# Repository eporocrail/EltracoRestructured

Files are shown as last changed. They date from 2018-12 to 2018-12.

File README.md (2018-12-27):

  Aim is to develop a switching and signaling system for model railroad track control.
  Communication is wireless.

  To disconnect the decoder from the controlling software in space and time the MOSQUITTO
  MQTT broker is used.

  Hardware setup is as simple as possible. In stead of having one hardware module for diffferent applications
  the design aims for three different PCB's specific to task where the Wemos has to be slotted into.

  Sofware is modularised. It is gathered into one software package. The functionality of each separate decoder
  is configured by means of a website genrated by the decoder.

  *********************************************************************************************

  Target platform is Wemos D1 mini.

  11 digital input/output pins, all pins have interrupt/pwm/I2C/one-wire supported(except D0)
  1 analog input(3.2V max input)
  a Micro USB connection
  compatible with Arduino IDE.
  pins are active LOW but the Arduino IDE inverts this.

  All of the IO pins run at 3.3V:
  A levelshifter or voltage divider is required.

  For a relay a pin is followed by a transistor/IC. A relay is driven with 5V.

  For a sensor or servo each pin is followed by a 330R resistor to limit current to 10 mA.

  eltraco decoder     Function

  eltraco sensor decoder    Scanning 9 sensors
  eltraco switch decoder    Controlling 8 outputs
  eltraco turnout decoder   Controlling 2 turnouts

  GPIO usage:

  Decoder  pins     function

  Sensor   D0 .. D7     digital sensor
  
           A0           analogue sensor

  Switch   D0 .. D7     output (switch)

  Double   D0    relais 1
  
  Turnout  D1    current detector 1
           
           D2    current detector 2
           
           D3    not used
           
           D4    not used
           
           D5    relais 2
           
           D6    servo 1
           
           D7    servo 2
           
           D8    not used
           
           A0    not used
           
  Single   D0    relais 1
  
  Turnout  D1    current detector 1
           
           D2    sensor
           
           D3    sensor
           
           D4    sensor
           
           D5    sensor
           
           D6    servo 1
           
           D7    not used
           
           D8    not used
           
           A0    not used         

  ROCNET PROTOCOL

  packet payload content:
  byte 1  : groupId
  
  byte 2  : receiveIdH
  
  byte 3  : receiveIdL
  
  byte 4  : sendIdH
  
  byte 5  : sendIdL
  
  byte 6  : group
  
  byte 7  : code
  
  byte 8  : length
  
  byte 9  : data1
  
  byte 10 : data2
  
  byte 11 : data3
  
  byte 12 : data4

  --byte 1 only used for large network. Normally 0.

  --byte 2 only used when more than 255 decoders. Normally 0.

  --byte 3 Rocrail Server default Id is 1

  Broadcast Id = 0
  
  Decoder   Id = 2 ... 255   Not used for switching decoder

  --byte 4 only used when more than 255 decoders. Normally 0.

  --byte 5 Rocrail Server default Id is 1

  Decoder Id   = 2 ... 255 with restrictions as described under "addressing"

  --byte 6

  groups
  code   description     remark                     MQTT topic
  
  0      Host            Rocrail                    rocnet/ht
  
  7      Clock Fast      Clock                      rocnet/ck
  
  8      Sensor          Position determination     rocnet/sr
  
  9      Output                                     rocnet/ot

  --byte 7

  Code:  bit 7 = 0
  
     bit 6 and bit 5 represent Type of code
     
     bit 4 .. 0:  5 bit command 0 .. 31

  Type: 0 - test
  
  1 - request
  
  2 - event
  
  3 - reply

  Sensor

  Actions
  code description data 1  data 2  data 3  data 4  data n
  1    report      addrH¹  addrL¹  status  port    identifier (RFID)

  ¹) Address of the reporting loco.
  The sensor ID is set in the header; Sender.

  Output

  Type   Value
  
  switch   0
  
  light    1
  
  servo    2

  Actions
  code description data 1  data 2  data 3
  
  0      off       type    value   address
  
  1      on        type    value   address

  --byte 8 Netto number of following data bytes.

  At a speed of 200 KmH a loc runs 64 mm per second in scale H0 and 35 mm per second in scale N.
  To come to a reliable detection reaction a point sensor must be scanned at least 20 times per second in H0
  and at least 10 times per second in scale N.

  For scale H0 scan delay should be not larger than 50 miliseconds and for scale N not larger
  than 100 miliseconds. Default will be 20.

  The Wemos Module needs no 3.3V power supply. To the 5V pin external powersupply can be connected.

  Addressing:

  Addressing falls apart in a WiFi address, being an IP-address and a Rocnet address.

  Rocnet:

  In the Rocnet protocol (IdH*256 + IdL) represents the Rocnet Node Number. This number ranges from 1 .. 65536.
  It represents the "Bus" number.
  Depending on the function performed the I/O pin of the decoder is addressed with "data3" for
  "output" functions or "data4" for "sensor" functions. Turnouts are controlled with an "output" function.
  The values of data3/data4 are in rocrail inserted in field "Address"

  For eltraco an I/O pin is addressed by the combination of receiveIdL and data3/data4.
  This way each individual pin of each individual decoder can be addressed.

  A second way to address an IO pin is using a "fixed" receiveIdL and discriminating by means of data3/data4.
  Using this method provides in eltraco the possibility to address 255 turnouts by a consecutive number only.
  The default receiveIdL of Rocrail is "9". This receiveIdL is used to control turnouts. These addresses are
  used by the servo-tool to adjust the servo of a turnout.

  IP-address:
  The following IP-adress range is available:
  192.168.xxx.xxx

  IP-addres: Router 192.168.xxx.251
  
             Configuration website 192.168.xxx.252
             
             Command Station       192.168.xxx.253
             
             Mosquitto             192.168.xxx.254

  For the decoders are available 192.168.xxx.2 - 192.168.2.250

  Each decoder is allocated a unique IP-address out of the range 192.168.xxx.2 - 192.168.2.250.
  The last triplet is the Rocrail "Bus" number.

  Single turnout decoder:

Each decoder controls 1 turnout and reports occupation of it.

For the turnout decoder occupation of the turnout is reported at "Address" 1.

Table: Switches tab Interface - the last part of the IP-address is inserted into field "Bus"
       "1" is inserted into field "Address".
       e.g. (192.168.0.154 turnout is inserted as Bus 154 Address 1)

Table: Sensor tab Interface - the last part of the IP-address is inserted into field "Bus"
       "1" is inserted into field "Address". The external sensors report using "Address" numbers 2 .. 5.
       e.g. (192.168.0.154 turnout is inserted as Bus 154 Address 1, the second external sensor of the same
       decoder is inserted as Bus 154 Address 3)

Double turnout decoder:

Each decoder controls 2 turnouts and reports occupation of them.

For the turnout decoder occupation of the first turnout is reported at "Address" 1 and of the second
turnout at "Address" 2.

Table: Switches tab Interface - the last part of the IP-address is inserted into field "Bus"
       For the first turnout "1" is inserted into field "Address". For the second one "2" is inserted
       e.g. (192.168.0.154 turnout 2 is inserted as Bus 154 Address 2)

Table: Sensor tab Interface - the last part of the IP-address is inserted into field "Bus"
       For the first turnout "1" is inserted into field "Address". For the second one "2" is inserted
       e.g. (192.168.0.154 turnout 2 is inserted as Bus 154 Address 2)

Operation

During testing it turned out that move orders from Rocrail arrived so fast that an ongoing movement was
interrupted. To cater for this, incoming turnout orders are stored into a buffer. When ongoing movement is concluded,
buffer content is converted into a turnout order and the next turnout starts moving.

Sensor decoder:
Each decoder has eight digital and one analogue sensor.

The sensors report using "Address" numbers 1 .. 9.
Use of the analogue sensor is to be programmed by the user.

Table: Sensor tab Interface - the last part of the IP-address is inserted into field "Bus"
       port number is inserted into field "Address"
       e.g. (192.168.0.076 sensor 5 is inserted as Bus 76 Address 5)

Operation

The state of the sensor is controlled by interrupt. Not only the state of the sensor but also the point in time of activation is stored.
If the sensor is still in the activated state after the debounce period has passed the Sensor Message is sent. 

The state of the sensor will change to "inactive" by interrupt. After the minimum activation time has passed this inactive state is signalled 

The state of the sensor will change to "inactive" by interrupt. After the minimum activation counts has passed this inactive state is signalled 

with a Sensor Message.

Interrupt reacts on changes to drive the sensor state.

D0 can NOT be used with Interrupt. This reduces the amount of interrupt driven sensors per module to 7. (D1 .. D7).

D0 has to be watched with "polling".

Switch decoder
Each decoder has eight outputs.

Each decoder is allocated a unique IP-address out of the range 192.168.xxx.2 - 192.168.2.250.
The last triplet is the Rocrail "Bus" number.

The outputs are switched using "Address" numbers 1 .. 8.

Table: Switches tab Interface - the last part of the IP-address is inserted into field "Bus"
       The individual port number is inserted into field "Address"
       e.g. (192.168.0.201 port 3 is inserted as Bus 201 Address 3)

Operation

Via configuration it is possible to have an output switched ON during 200 mSec. An additional relais attached to that
output can be used to control a solenoid activated device.

To signal the state of a switch, a sensor message is transmitted after each switch action. 

Configuration of decoder

The Wemos module can be used in "ST" mode and "AP" mode simultaneously.
In "ST" mode it is possible to login onto an existing WiFi network for normal operations.
In "AP" mode it is possible to generate its own WiFi network. This network is used for configuration of the decoder.
Each module has its own configuration webserver on a shared WiFi configuration network with its own IP address.

The websever is based on the "EmbAJAX" library. This library facilitates dataexchange between webserver on the decoder
and a browser on a client. The user experience is as much as possible comparable with webservers on PC like hardware.

Configuration data and servo angles are stored in EEPROM.
Allocation of EEPROM memory to variables has to be planned.
  location variable
      0    AngleA1
      1    AngleB1
      2    Delay1
      3    Swap1
      4    AngleA2
      5    AngleB2
      6    Delay2
      7    Swap2
      8    decoderType
      9    debugFlag

  GENERALOFFSET+ 0 .. 25 ST WiFi SSID
  
  GENERALOFFSET + SSIDOFFSET + 0 .. 8 ST WiFi Password
  
  GENERALOFFSET + SSIDOFFSET + PWDOFFSET + 0 .. 6 ST WiFi IP address triplets
  
  GENERALOFFSET + SSIDOFFSET + PWDOFFSET + IPOFFSET + 0 .. 8 Output puls 
  
  GENERALOFFSET + SSIDOFFSET + PWDOFFSET + IPOFFSET + OUTPUTOFFSET + 0 .. 8 Switch active puls length

Configuration data and servo angles are stored in EEPROM.
Allocation of EEPROM memory to variables has to be planned.
  location variable
      0    AngleA1
      1    AngleB1
      2    Delay1
      3 .  Swap1
      4    AngleA2
      5    AngleB2
      6    Delay2
      7 .  Swap2
      8    decoderType
      9    debugFlag

  GENERALOFFSET+ 0 .. 25 ST WiFi SSID
  
  GENERALOFFSET + SSIDOFFSET + 0 .. 8 ST WiFi Password
  
  GENERALOFFSET + SSIDOFFSET + PWDOFFSET `+ 0 .. 6 ST WiFi IP address triplets
  
  GENERALOFFSET + SSIDOFFSET + PWDOFFSET + IPOFFSET + 0 .. 8 Output puls 
  
  GENERALOFFSET + SSIDOFFSET + PWDOFFSET + IPOFFSET + OUTPUTOFFSET + 0 .. 8 Switch active puls length 
  
  GENERALOFFSET + SSIDOFFSET + PWDOFFSET + IPOFFSET + OUTPUTOFFSET + PULSLENGTHOFFSET+ 0 .. 8 Output sensor message

  GENERALOFFSET      - 20
  SSIDOFFSET         - 30
  PWDOFFSET          - 20
  IPOFFSET           - 10
  OUTPUTOFFSET        -10
  PULSLENGTHOFFSET    -20
  OUTPUTSENSOROFFSET  -10

The ST WiFi password is generated out of "ELTRACO" and the decoderId.
The AP WiFi SSID is generated out of "ELTRACO" and the decoderID. This also aplies to the related password.

There are two ways to transfer Software to the decoder.
Via USB cable and after inital software installation also "Over The Air"(OTA).
Each decoder has its own OTA name which is generated outof "ELTRACO" and the decoderId.

Author: E. Postma

November 2018

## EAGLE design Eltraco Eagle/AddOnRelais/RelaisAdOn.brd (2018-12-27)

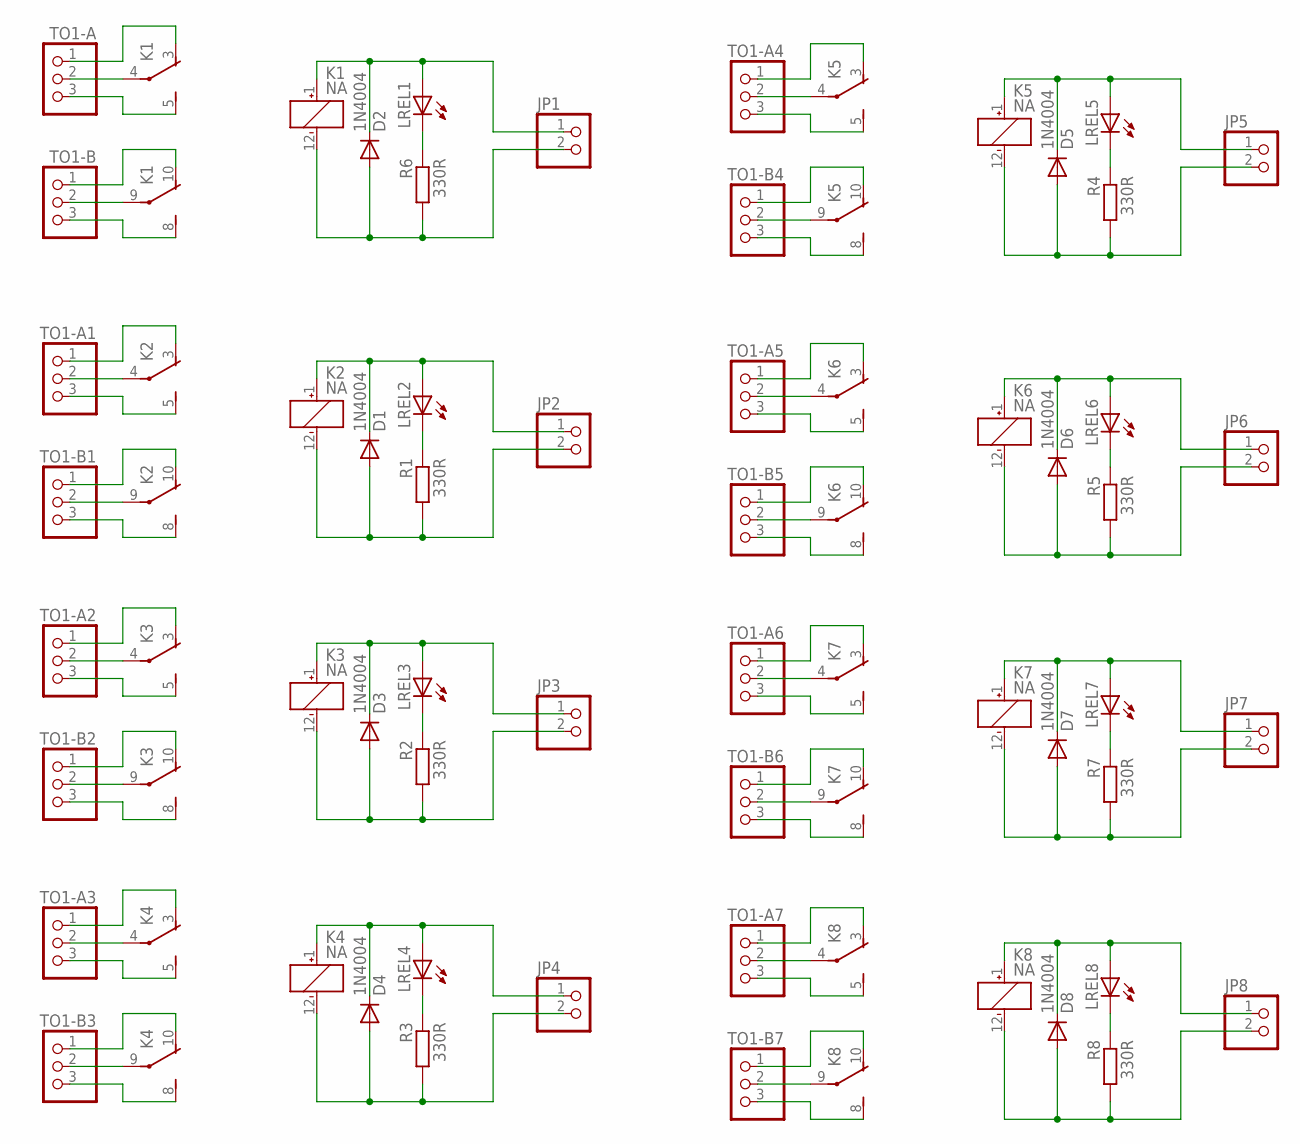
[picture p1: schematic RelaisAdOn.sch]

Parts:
D1, D2, D3, D4, D5, D6, D7, D8: 1N4004; DO41-10
JP1, JP2, JP3, JP4, JP5, JP6, JP7, JP8: PINHD-1X2; 1X02
K1, K2, K3, K4, K5, K6, K7, K8: NA
LREL1, LREL2, LREL3, LREL4, LREL5, LREL6, LREL7, LREL8: LED3MM
R1, R2, R3, R4, R5, R6, R7, R8: 330R; 0207/7
TO1-A, TO1-A1, TO1-A2, TO1-A3, TO1-A4, TO1-A5, TO1-A6, TO1-A7, TO1-B, TO1-B1, TO1-B2, TO1-B3, TO1-B4, TO1-B5, TO1-B6, TO1-B7: PINHD-1X3; 1X03

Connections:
unnamed: K1.4, TO1-A.2
unnamed: LREL1.K (C), R6.1
unnamed: K1.9, TO1-B.2
unnamed: K1.8 (S), TO1-B.3
unnamed: K1.10 (O), TO1-B.1
unnamed: K1.3 (O), TO1-A.1
unnamed: K1.5 (S), TO1-A.3
unnamed: D2.A, JP1.2, K1.12 (-), R6.2
unnamed: D2.C, JP1.1, K1.1 (+), LREL1.A
unnamed: LREL2.K (C), R1.1
unnamed: D1.A, JP2.2, K2.12 (-), R1.2
unnamed: D1.C, JP2.1, K2.1 (+), LREL2.A
unnamed: K2.4, TO1-A1.2
unnamed: K2.9, TO1-B1.2
unnamed: K2.8 (S), TO1-B1.3
unnamed: K2.10 (O), TO1-B1.1
unnamed: K2.3 (O), TO1-A1.1
unnamed: K2.5 (S), TO1-A1.3
unnamed: LREL3.K (C), R2.1
unnamed: D3.A, JP3.2, K3.12 (-), R2.2
unnamed: D3.C, JP3.1, K3.1 (+), LREL3.A
unnamed: K3.4, TO1-A2.2
unnamed: K3.9, TO1-B2.2
unnamed: K3.8 (S), TO1-B2.3
unnamed: K3.10 (O), TO1-B2.1
unnamed: K3.3 (O), TO1-A2.1
unnamed: K3.5 (S), TO1-A2.3
unnamed: LREL4.K (C), R3.1
unnamed: D4.A, JP4.2, K4.12 (-), R3.2
unnamed: D4.C, JP4.1, K4.1 (+), LREL4.A
unnamed: K4.4, TO1-A3.2
unnamed: K4.9, TO1-B3.2
unnamed: K4.8 (S), TO1-B3.3
unnamed: K4.10 (O), TO1-B3.1
unnamed: K4.3 (O), TO1-A3.1
unnamed: K4.5 (S), TO1-A3.3
unnamed: LREL5.K (C), R4.1
unnamed: D5.A, JP5.2, K5.12 (-), R4.2
unnamed: D5.C, JP5.1, K5.1 (+), LREL5.A
unnamed: K5.4, TO1-A4.2
unnamed: K5.9, TO1-B4.2
unnamed: K5.8 (S), TO1-B4.3
unnamed: K5.10 (O), TO1-B4.1
unnamed: K5.3 (O), TO1-A4.1
unnamed: K5.5 (S), TO1-A4.3
unnamed: LREL6.K (C), R5.1
unnamed: D6.A, JP6.2, K6.12 (-), R5.2
unnamed: D6.C, JP6.1, K6.1 (+), LREL6.A
unnamed: K6.4, TO1-A5.2
unnamed: K6.9, TO1-B5.2
unnamed: K6.8 (S), TO1-B5.3
unnamed: K6.10 (O), TO1-B5.1
unnamed: K6.3 (O), TO1-A5.1
unnamed: K6.5 (S), TO1-A5.3
unnamed: LREL7.K (C), R7.1
unnamed: D7.A, JP7.2, K7.12 (-), R7.2
unnamed: D7.C, JP7.1, K7.1 (+), LREL7.A
unnamed: K7.4, TO1-A6.2
unnamed: K7.9, TO1-B6.2
unnamed: K7.8 (S), TO1-B6.3
unnamed: K7.10 (O), TO1-B6.1
unnamed: K7.3 (O), TO1-A6.1
unnamed: K7.5 (S), TO1-A6.3
unnamed: LREL8.K (C), R8.1
unnamed: D8.A, JP8.2, K8.12 (-), R8.2
unnamed: D8.C, JP8.1, K8.1 (+), LREL8.A
unnamed: K8.4, TO1-A7.2
unnamed: K8.9, TO1-B7.2
unnamed: K8.8 (S), TO1-B7.3
unnamed: K8.10 (O), TO1-B7.1
unnamed: K8.3 (O), TO1-A7.1
unnamed: K8.5 (S), TO1-A7.3

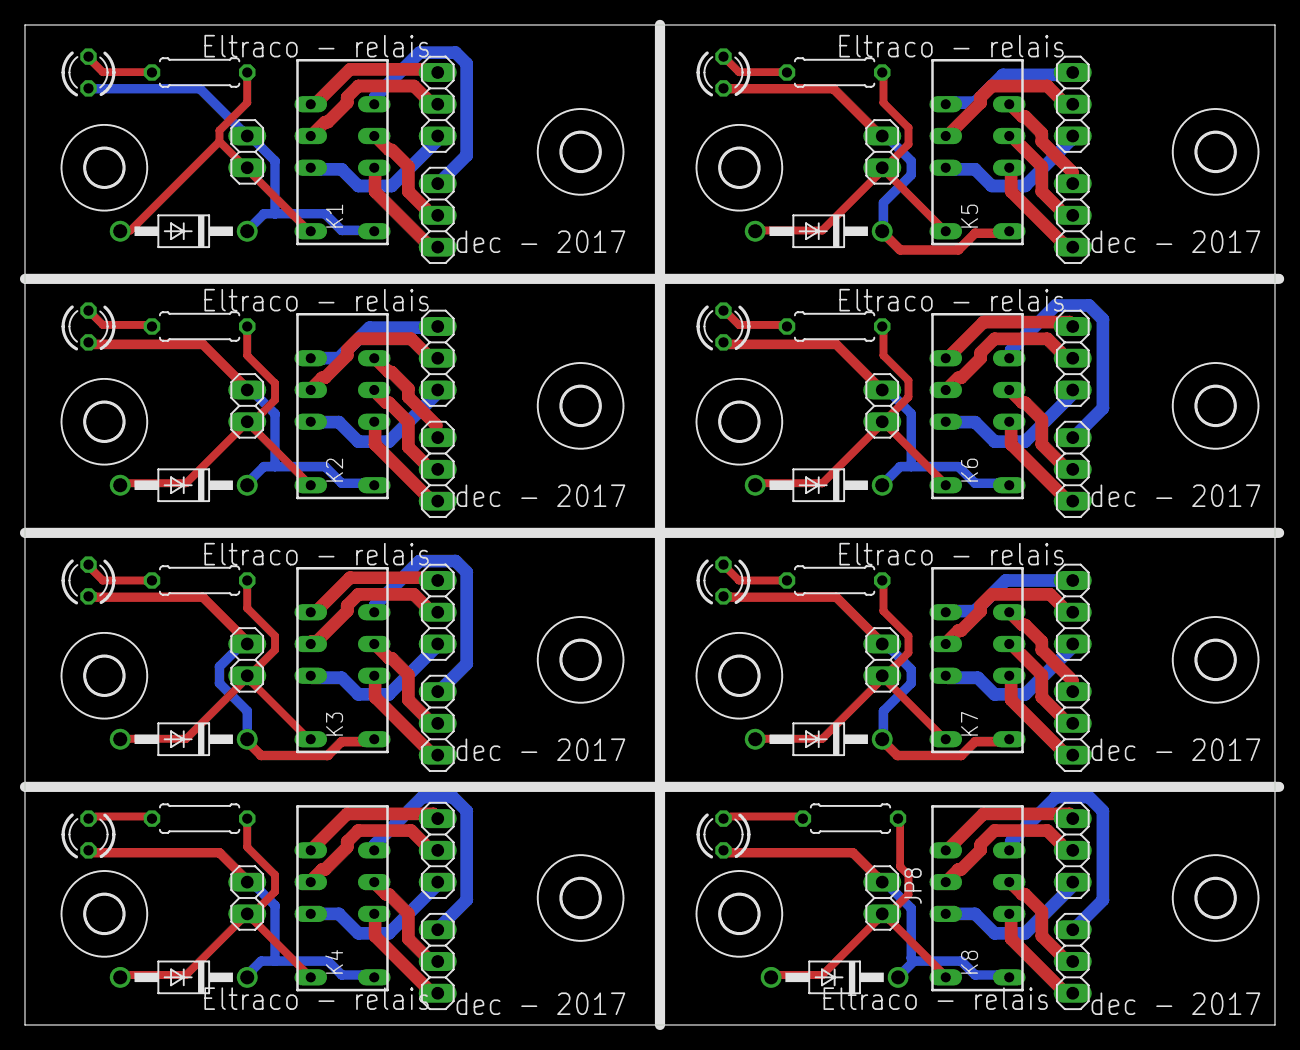
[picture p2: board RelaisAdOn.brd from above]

Board: 2 copper layers, 100.0 x 80.0 mm, 72 parts (0 on the bottom side), 72 nets.

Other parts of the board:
U$1, U$2, U$3, U$4, U$5, U$6, U$7, U$8, U$9, U$10, U$11, U$12, U$13, U$14, U$15, U$16: 3,0

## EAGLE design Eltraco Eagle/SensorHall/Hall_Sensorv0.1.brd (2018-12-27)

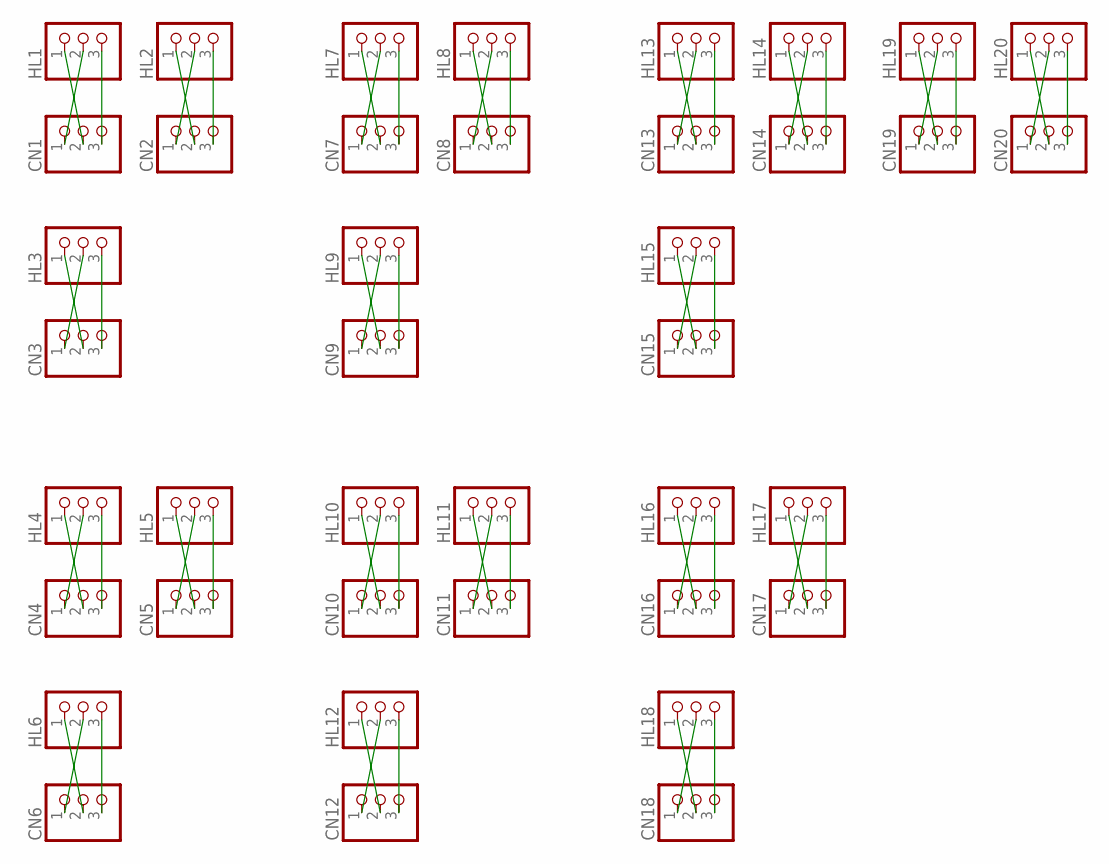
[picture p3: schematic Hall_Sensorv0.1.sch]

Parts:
CN1, CN2, CN3, CN4, CN5, CN6, CN7, CN8, CN9, CN10, CN11, CN12, CN13, CN14, CN15, CN16, CN17, CN18, CN19, CN20: PINHD-1X3; 1X03
HL1, HL2, HL3, HL4, HL5, HL6, HL7, HL8, HL9, HL10, HL11, HL12, HL13, HL14, HL15, HL16, HL17, HL18, HL19, HL20: PINHD-1X3; 1X03

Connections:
unnamed: CN1.1, HL1.2
unnamed: CN1.2, HL1.1
unnamed: CN7.3, HL7.3
unnamed: CN2.2, HL2.1
unnamed: CN2.1, HL2.2
unnamed: CN8.3, HL8.3
unnamed: CN7.2, HL7.1
unnamed: CN7.1, HL7.2
unnamed: CN9.3, HL9.3
unnamed: CN8.2, HL8.1
unnamed: CN8.1, HL8.2
unnamed: CN10.3, HL10.3
unnamed: CN13.2, HL13.1
unnamed: CN13.1, HL13.2
unnamed: CN11.3, HL11.3
unnamed: CN14.2, HL14.1
unnamed: CN14.1, HL14.2
unnamed: CN12.3, HL12.3
unnamed: CN19.2, HL19.1
unnamed: CN19.1, HL19.2
unnamed: CN13.3, HL13.3
unnamed: CN20.2, HL20.1
unnamed: CN20.1, HL20.2
unnamed: CN14.3, HL14.3
unnamed: CN15.2, HL15.1
unnamed: CN15.1, HL15.2
unnamed: CN15.3, HL15.3
unnamed: CN9.2, HL9.1
unnamed: CN9.1, HL9.2
unnamed: CN16.3, HL16.3
unnamed: CN3.2, HL3.1
unnamed: CN3.1, HL3.2
unnamed: CN17.3, HL17.3
unnamed: CN4.2, HL4.1
unnamed: CN4.1, HL4.2
unnamed: CN18.3, HL18.3
unnamed: CN5.2, HL5.1
unnamed: CN5.1, HL5.2
unnamed: CN19.3, HL19.3
unnamed: CN10.2, HL10.1
unnamed: CN10.1, HL10.2
unnamed: CN11.2, HL11.1
unnamed: CN20.3, HL20.3
unnamed: CN11.1, HL11.2
unnamed: CN1.3, HL1.3
unnamed: CN16.2, HL16.1
unnamed: CN16.1, HL16.2
unnamed: CN17.2, HL17.1
unnamed: CN17.1, HL17.2
unnamed: CN6.2, HL6.1
unnamed: CN2.3, HL2.3
unnamed: CN6.1, HL6.2
unnamed: CN12.2, HL12.1
unnamed: CN12.1, HL12.2
unnamed: CN3.3, HL3.3
unnamed: CN18.2, HL18.1
unnamed: CN18.1, HL18.2
unnamed: CN4.3, HL4.3
unnamed: CN5.3, HL5.3
unnamed: CN6.3, HL6.3

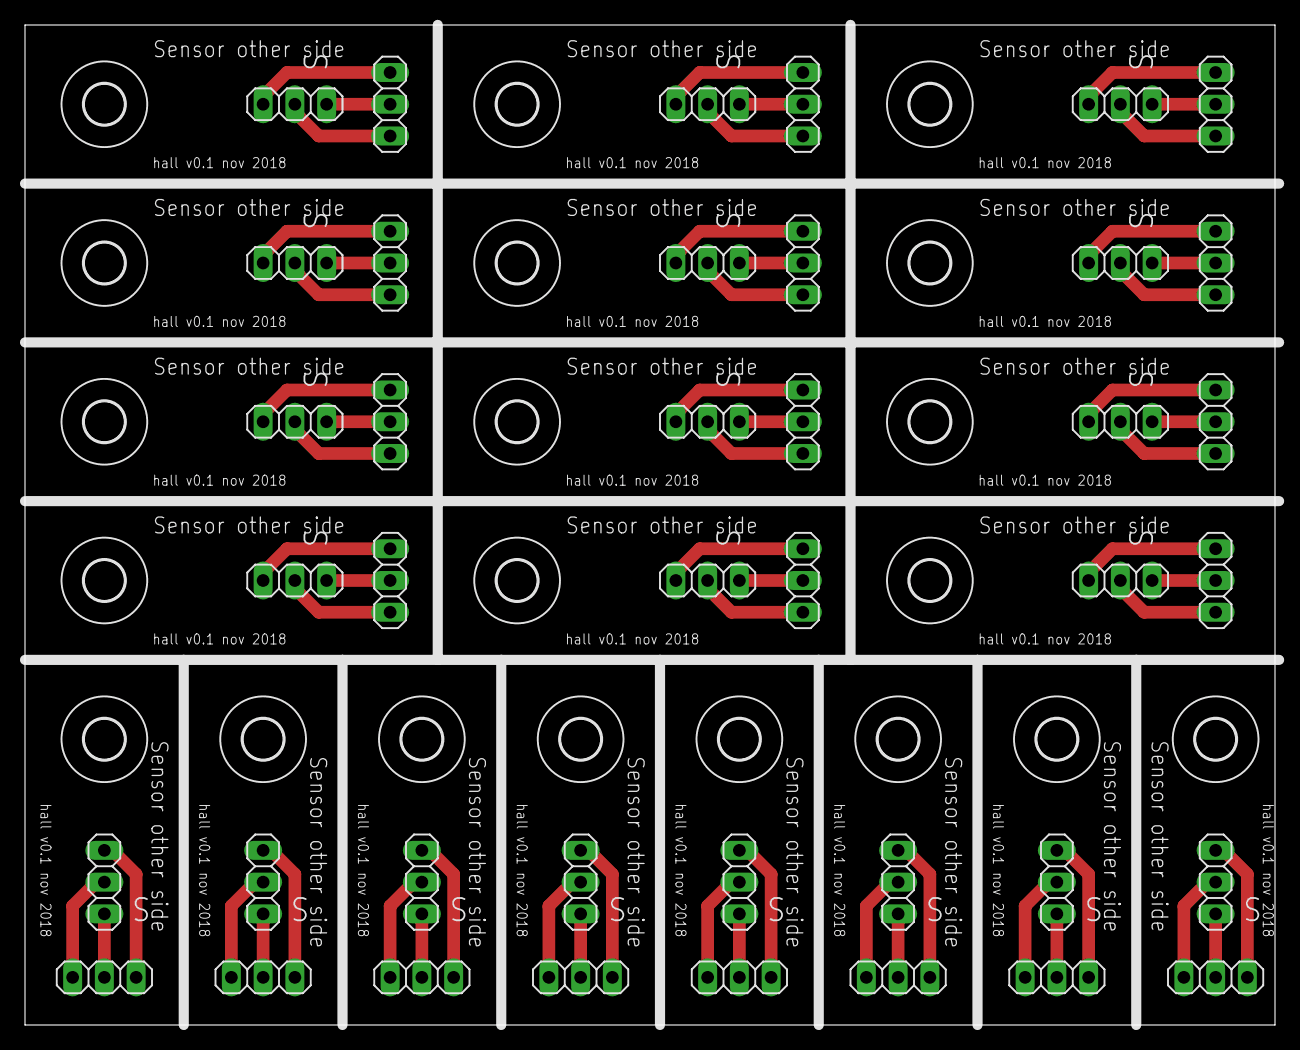
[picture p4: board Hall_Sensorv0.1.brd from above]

Board: 2 copper layers, 100.0 x 80.0 mm, 60 parts (0 on the bottom side), 60 nets.

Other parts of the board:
U$1, U$2, U$3, U$4, U$5, U$6, U$7, U$8, U$9, U$10, U$11, U$12, U$13, U$14, U$15, U$16, U$17, U$18, U$19, U$20: 3,2

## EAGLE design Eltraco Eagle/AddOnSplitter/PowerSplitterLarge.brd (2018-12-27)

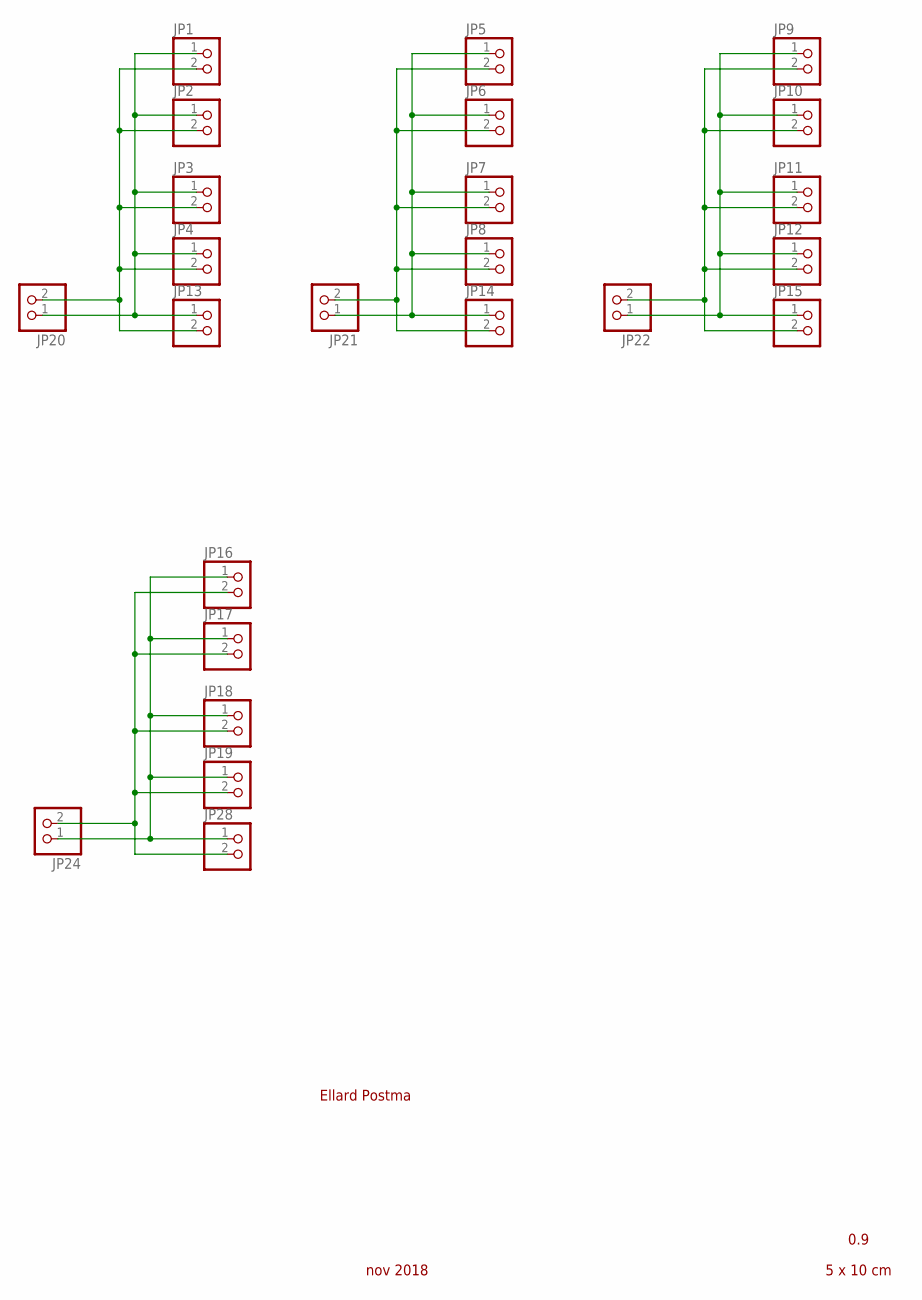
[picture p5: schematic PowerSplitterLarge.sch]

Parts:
JP1, JP2, JP3, JP4, JP5, JP6, JP7, JP8, JP9, JP10, JP11, JP12, JP13, JP14, JP15, JP16, JP17, JP18, JP19, JP20, JP21, JP22, JP24, JP28: PINHD-1X2/90; 1X02/90

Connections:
G1: JP1.2, JP2.2, JP3.2, JP4.2, JP13.2, JP20.2
G2: JP5.2, JP6.2, JP7.2, JP8.2, JP14.2, JP21.2
G3: JP9.2, JP10.2, JP11.2, JP12.2, JP15.2, JP22.2
G4: JP16.2, JP17.2, JP18.2, JP19.2, JP24.2, JP28.2
PLUS: JP1.1, JP2.1, JP3.1, JP4.1, JP13.1, JP20.1
PLUS2: JP5.1, JP6.1, JP7.1, JP8.1, JP14.1, JP21.1
PLUS3: JP9.1, JP10.1, JP11.1, JP12.1, JP15.1, JP22.1
PLUS4: JP16.1, JP17.1, JP18.1, JP19.1, JP24.1, JP28.1

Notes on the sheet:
Ellard Postma
nov 2018
5 x 10 cm
0.9

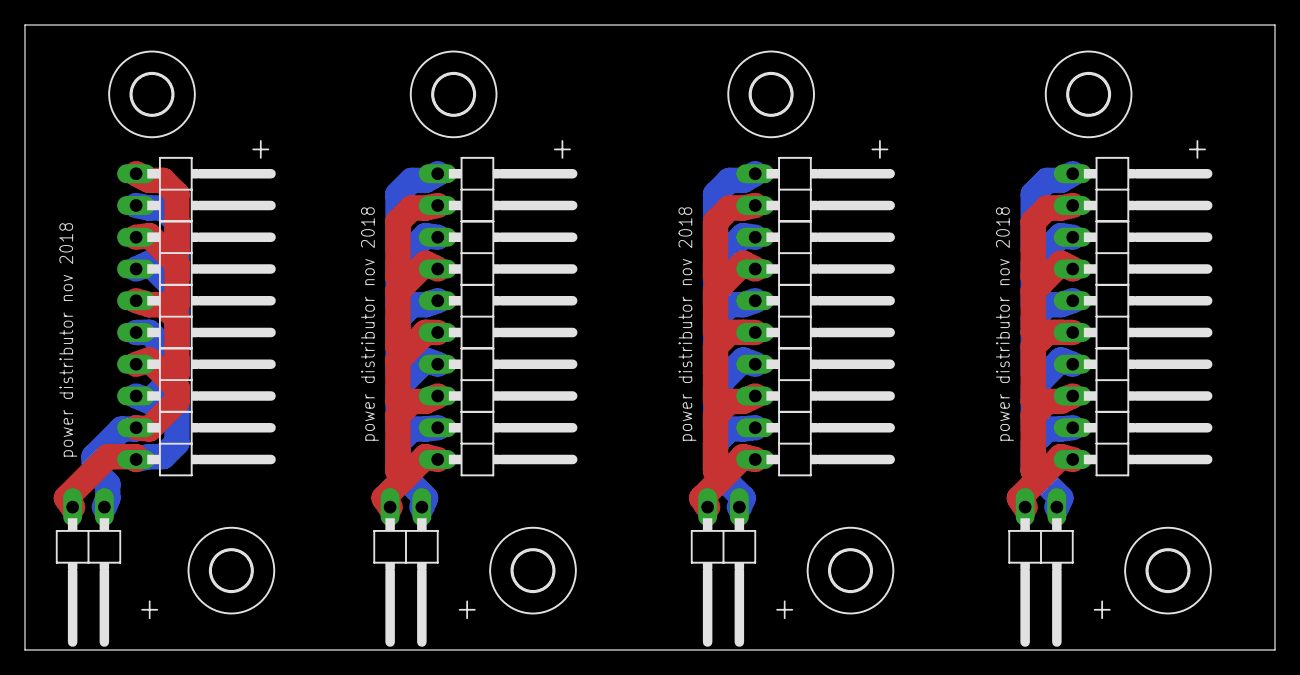
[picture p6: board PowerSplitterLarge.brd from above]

Board: 2 copper layers, 100.0 x 50.0 mm, 32 parts (0 on the bottom side), 8 nets.

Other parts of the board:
U$1, U$2, U$3, U$4, U$5, U$6, U$7, U$8: 3,2

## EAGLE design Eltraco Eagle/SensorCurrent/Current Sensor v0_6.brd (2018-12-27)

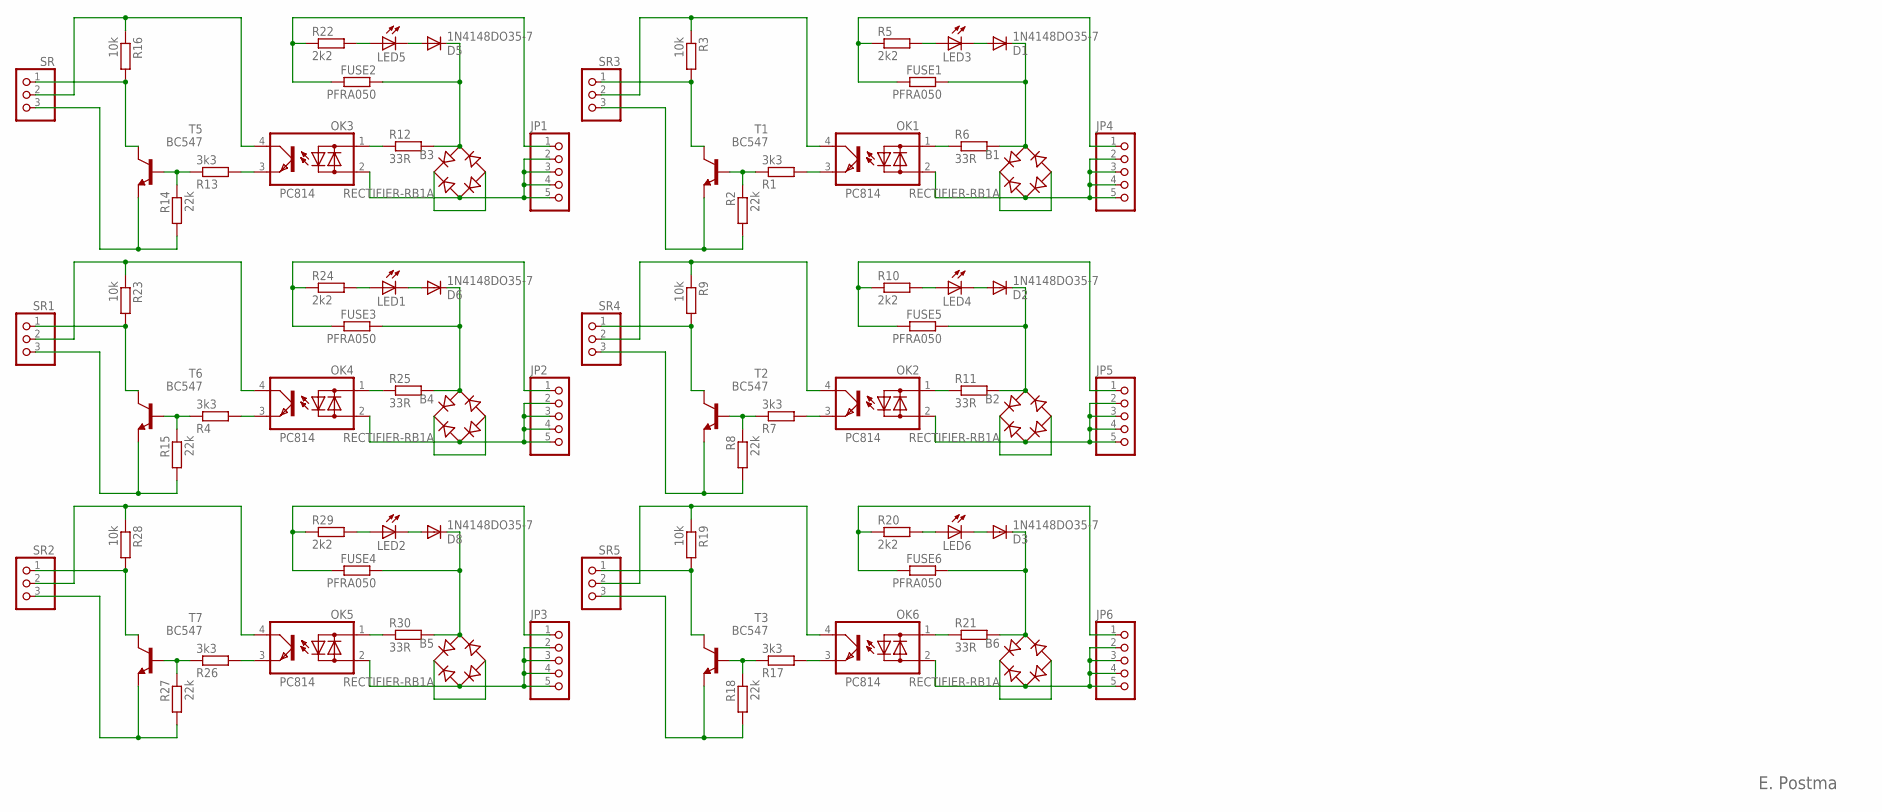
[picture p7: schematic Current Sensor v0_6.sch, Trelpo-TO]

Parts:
B1, B2, B3, B4, B5, B6: RECTIFIER-RB1A; RB1A
D1, D2, D3, D5, D6, D8: 1N4148DO35-7; DO35-7
FUSE1, FUSE2, FUSE3, FUSE4, FUSE5, FUSE6: PFRA050; 0414V
JP1, JP2, JP3, JP4, JP5, JP6: PINHD-1X5; 1X05
LED1, LED2, LED3, LED4, LED5, LED6: LED3MM
OK1, OK2, OK3, OK4, OK5, OK6: PC814; DIL04
R1, R4, R7, R13, R17, R26: 3k3; 0207/7
R2, R8, R14, R15, R18, R27: 22k; 0207/7
R3, R9, R16, R19, R23, R28: 10k; 0207/7
R5, R10, R20, R22, R24, R29: 2k2; 0207/7
R6, R11, R12, R21, R25, R30: 33R; 0207/7
SR, SR1, SR2, SR3, SR4, SR5: PINHD-1X3; 1X03
T1, T2, T3, T5, T6, T7: BC547; TO92

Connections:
unnamed: OK3.1 (AC1), R12.1
unnamed: OK1.1 (AC1), R6.1
unnamed: LED3.A, R5.2
unnamed: D1.A, LED3.K (C)
unnamed: B1.AC1, D1.C, FUSE1.1, R6.2
unnamed: B1.+, B1.-
unnamed: FUSE1.2, JP4.1, R5.1
unnamed: B1.AC2, JP4.2, JP4.3, JP4.4, JP4.5, OK1.2 (AC2)
unnamed: R1.1, R2.1, T1.2 (B)
unnamed: R3.2, SR3.1, T1.3 (C)
unnamed: OK1.3 (E), R1.2
unnamed: OK1.4 (C), R3.1, SR3.2
unnamed: R2.2, SR3.3, T1.1 (E)
unnamed: OK2.1 (AC1), R11.1
unnamed: LED4.A, R10.2
unnamed: D2.A, LED4.K (C)
unnamed: B2.AC1, D2.C, FUSE5.1, R11.2
unnamed: B2.+, B2.-
unnamed: FUSE5.2, JP5.1, R10.1
unnamed: B2.AC2, JP5.2, JP5.3, JP5.4, JP5.5, OK2.2 (AC2)
unnamed: R7.1, R8.1, T2.2 (B)
unnamed: R9.2, SR4.1, T2.3 (C)
unnamed: OK2.3 (E), R7.2
unnamed: LED5.A, R22.2
unnamed: D5.A, LED5.K (C)
unnamed: OK2.4 (C), R9.1, SR4.2
unnamed: R8.2, SR4.3, T2.1 (E)
unnamed: OK6.1 (AC1), R21.1
unnamed: LED6.A, R20.2
unnamed: B3.AC1, D5.C, FUSE2.1, R12.2
unnamed: D3.A, LED6.K (C)
unnamed: B6.AC1, D3.C, FUSE6.1, R21.2
unnamed: B6.+, B6.-
unnamed: FUSE6.2, JP6.1, R20.1
unnamed: B6.AC2, JP6.2, JP6.3, JP6.4, JP6.5, OK6.2 (AC2)
unnamed: B3.+, B3.-
unnamed: FUSE2.2, JP1.1, R22.1
unnamed: R13.1, R14.1, T5.2 (B)
unnamed: R16.2, SR.1, T5.3 (C)
unnamed: B3.AC2, JP1.2, JP1.3, JP1.4, JP1.5, OK3.2 (AC2)
unnamed: R17.1, R18.1, T3.2 (B)
unnamed: R19.2, SR5.1, T3.3 (C)
unnamed: OK3.3 (E), R13.2
unnamed: OK4.1 (AC1), R25.1
unnamed: OK3.4 (C), R16.1, SR.2
unnamed: OK6.3 (E), R17.2
unnamed: LED1.A, R24.2
unnamed: D6.A, LED1.K (C)
unnamed: OK6.4 (C), R19.1, SR5.2
unnamed: R18.2, SR5.3, T3.1 (E)
unnamed: B4.AC1, D6.C, FUSE3.1, R25.2
unnamed: B4.+, B4.-
unnamed: FUSE3.2, JP2.1, R24.1
unnamed: B4.AC2, JP2.2, JP2.3, JP2.4, JP2.5, OK4.2 (AC2)
unnamed: R4.1, R15.1, T6.2 (B)
unnamed: R23.2, SR1.1, T6.3 (C)
unnamed: OK4.3 (E), R4.2
unnamed: OK4.4 (C), R23.1, SR1.2
unnamed: R14.2, SR.3, T5.1 (E)
unnamed: R15.2, SR1.3, T6.1 (E)
unnamed: OK5.1 (AC1), R30.1
unnamed: LED2.A, R29.2
unnamed: D8.A, LED2.K (C)
unnamed: B5.AC1, D8.C, FUSE4.1, R30.2
unnamed: B5.+, B5.-
unnamed: FUSE4.2, JP3.1, R29.1
unnamed: B5.AC2, JP3.2, JP3.3, JP3.4, JP3.5, OK5.2 (AC2)
unnamed: R26.1, R27.1, T7.2 (B)
unnamed: R28.2, SR2.1, T7.3 (C)
unnamed: OK5.3 (E), R26.2
unnamed: OK5.4 (C), R28.1, SR2.2
unnamed: R27.2, SR2.3, T7.1 (E)

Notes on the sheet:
E. Postma

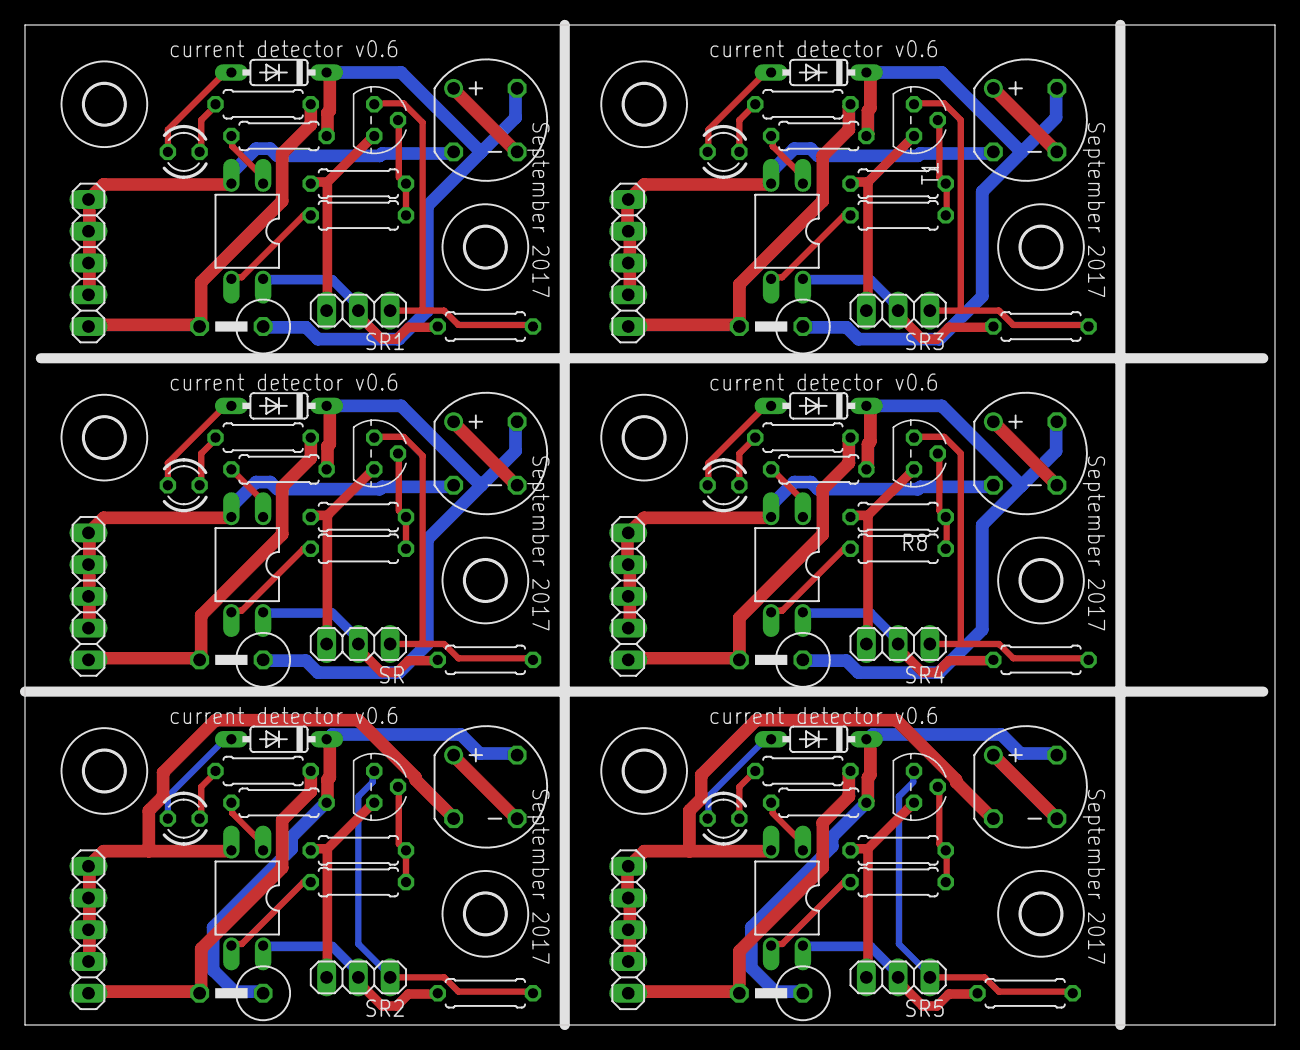
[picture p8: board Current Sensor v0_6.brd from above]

Board: 2 copper layers, 100.0 x 80.0 mm, 90 parts (0 on the bottom side), 72 nets.

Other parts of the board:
U$1, U$2, U$3, U$4, U$5, U$6, U$7, U$8, U$9, U$10, U$11, U$12: 3,2

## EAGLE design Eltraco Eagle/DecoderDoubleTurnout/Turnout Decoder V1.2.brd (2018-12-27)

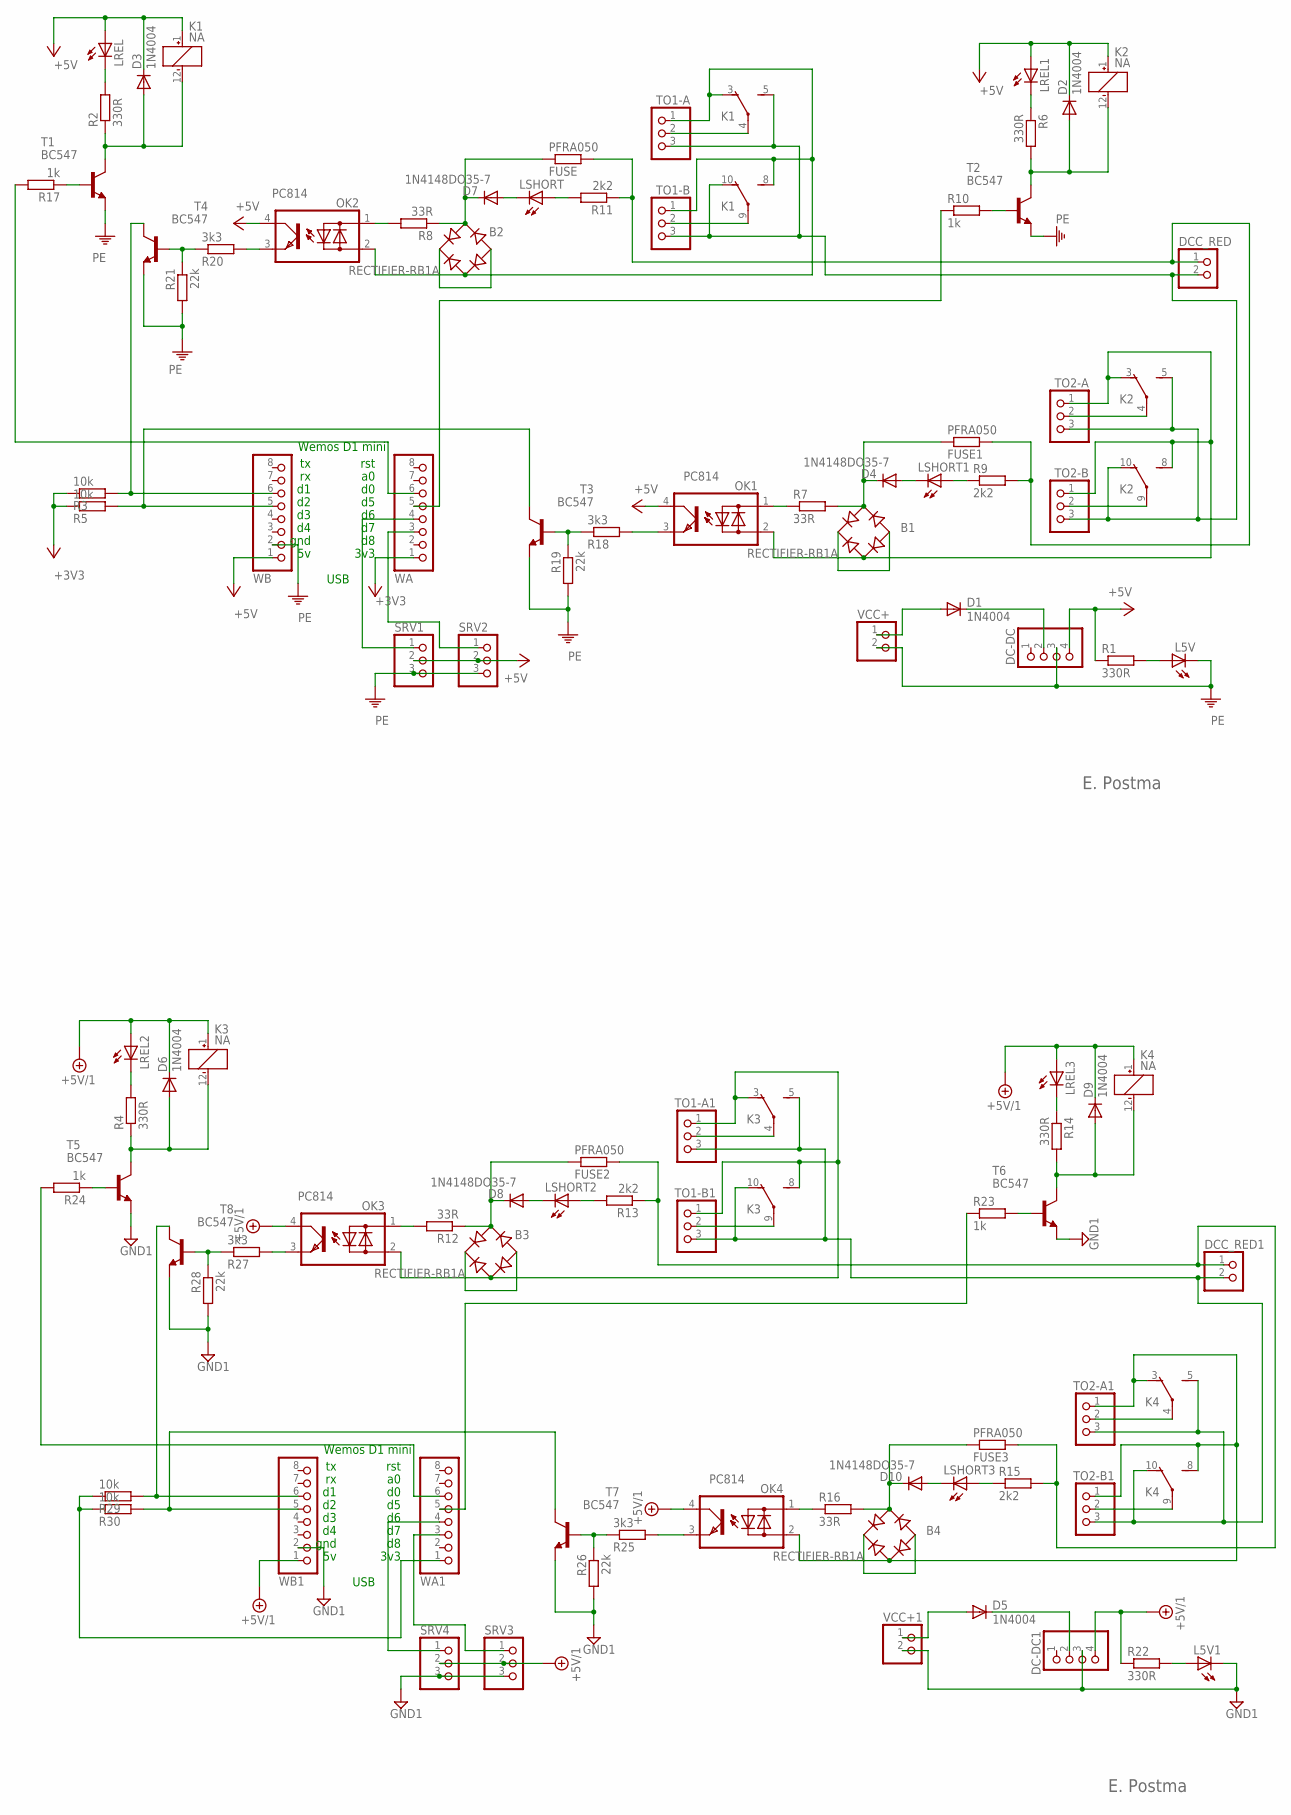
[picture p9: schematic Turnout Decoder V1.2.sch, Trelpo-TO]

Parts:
B1, B2, B3, B4: RECTIFIER-RB1A; RB1A
D1, D2, D3, D5, D6, D9: 1N4004; DO41-10
D4, D7, D8, D10: 1N4148DO35-7; DO35-7
DC-DC, DC-DC1: PINHD-1X4; 1X04
DCC_RED, DCC_RED1: PINHD-1X2; 1X02
FUSE, FUSE1, FUSE2, FUSE3: PFRA050; 0414V
K1, K2, K3, K4: NA
L5V, L5V1: LED3MM
LREL, LREL1, LREL2, LREL3: LED3MM
LSHORT, LSHORT1, LSHORT2, LSHORT3: LED3MM
OK1, OK2, OK3, OK4: PC814; DIL04
R1, R2, R4, R6, R14, R22: 330R; 0207/7
R3, R5, R29, R30: 10k; 0207/7
R7, R8, R12, R16: 33R; 0207/7
R9, R11, R13, R15: 2k2; 0207/7
R10, R17, R23, R24: 1k; 0207/7
R18, R20, R25, R27: 3k3; 0207/7
R19, R21, R26, R28: 22k; 0207/7
SRV1, SRV2, SRV3, SRV4: PINHD-1X3; 1X03
T1, T2, T3, T4, T5, T6, T7, T8: BC547; TO92
TO1-A, TO1-A1, TO1-B, TO1-B1, TO2-A, TO2-A1, TO2-B, TO2-B1: PINHD-1X3; 1X03
VCC+, VCC+1: PINHD-1X2; 1X02
WA, WA1: PINHD-1X8; 1X08
WB, WB1: PINHD-1X8; 1X08

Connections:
+3V3: R3.1, R5.1, WA.1
+5V: D2.C, D3.C, DC-DC.4, K1.1 (+), K2.1 (+), LREL.A, LREL1.A, OK1.4 (C), OK2.4 (C), R1.1, SRV1.2, SRV2.2, WB.1
+5V/1: D6.C, D9.C, DC-DC1.4, K3.1 (+), K4.1 (+), LREL2.A, LREL3.A, OK3.4 (C), OK4.4 (C), R22.1, SRV3.2, SRV4.2, WB1.1
GND1: DC-DC1.3, L5V1.K (C), R26.2, R28.2, SRV3.3, SRV4.3, T5.1 (E), T6.1 (E), T7.1 (E), T8.1 (E), VCC+1.2, WB1.2
unnamed: LREL2.K (C), R4.2
unnamed: LREL1.K (C), R6.1
unnamed: DCC_RED.1, FUSE.2, FUSE1.2, R9.2, R11.1
unnamed: D1.A, VCC+.1
unnamed: OK1.1 (AC1), R7.1
unnamed: LSHORT1.A, R9.1
unnamed: D4.A, LSHORT1.K (C)
unnamed: D2.A, K2.12 (-), R6.2, T2.3 (C)
unnamed: R10.2, T2.2 (B)
unnamed: B1.+, B1.-
unnamed: OK1.3 (E), R18.2
unnamed: LREL.K (C), R2.2
unnamed: K2.4, TO2-A.2
unnamed: B2.AC2, K1.3 (O), K1.8 (S), OK2.2 (AC2), TO1-A.1, TO1-B.1
unnamed: K2.9, TO2-B.2
unnamed: DCC_RED.2, K1.5 (S), K1.10 (O), K2.5 (S), K2.10 (O), TO1-A.3, TO1-B.3, TO2-A.3, TO2-B.3
unnamed: OK2.3 (E), R20.2
unnamed: B1.AC2, K2.3 (O), K2.8 (S), OK1.2 (AC2), TO2-A.1, TO2-B.1
unnamed: R3.2, T4.3 (C), WB.6
unnamed: B1.AC1, D4.C, FUSE1.1, R7.2
unnamed: OK2.1 (AC1), R8.2
unnamed: R5.2, T3.3 (C), WB.5
unnamed: B2.AC1, D7.C, FUSE.1, R8.1
unnamed: OK3.1 (AC1), R12.2
unnamed: LSHORT2.A, R13.2
unnamed: K1.4, TO1-A.2
unnamed: R18.1, R19.1, T3.2 (B)
unnamed: R20.1, R21.1, T4.2 (B)
unnamed: R17.2, WA.6
unnamed: D8.A, LSHORT2.K (C)
unnamed: SRV1.1, WA.4
unnamed: K1.9, TO1-B.2
unnamed: SRV2.1, WA.3
unnamed: R10.1, WA.5
unnamed: LSHORT.A, R11.2
unnamed: D6.A, K3.12 (-), R4.1, T5.3 (C)
unnamed: R24.1, T5.2 (B)
unnamed: B3.+, B3.-
unnamed: L5V1.A, R22.2
unnamed: D5.A, VCC+1.1
unnamed: D7.A, LSHORT.K (C)
unnamed: B2.+, B2.-
unnamed: D5.C, DC-DC1.2
unnamed: K3.4, TO1-A1.2
unnamed: K3.9, TO1-B1.2
unnamed: L5V.A, R1.2
unnamed: B3.AC2, K3.3 (O), K3.8 (S), OK3.2 (AC2), TO1-A1.1, TO1-B1.1
unnamed: B3.AC1, D8.C, FUSE2.1, R12.1
unnamed: R17.1, T1.2 (B)
unnamed: D3.A, K1.12 (-), R2.1, T1.3 (C)
unnamed: LREL3.K (C), R14.1
unnamed: OK4.1 (AC1), R16.1
unnamed: LSHORT3.A, R15.1
unnamed: D10.A, LSHORT3.K (C)
unnamed: D9.A, K4.12 (-), R14.2, T6.3 (C)
unnamed: R23.2, T6.2 (B)
unnamed: B4.+, B4.-
unnamed: D1.C, DC-DC.2
unnamed: K4.4, TO2-A1.2
unnamed: K4.9, TO2-B1.2
unnamed: DCC_RED1.2, K3.5 (S), K3.10 (O), K4.5 (S), K4.10 (O), TO1-A1.3, TO1-B1.3, TO2-A1.3, TO2-B1.3
unnamed: B4.AC2, K4.3 (O), K4.8 (S), OK4.2 (AC2), TO2-A1.1, TO2-B1.1
unnamed: B4.AC1, D10.C, FUSE3.1, R16.2
unnamed: DCC_RED1.1, FUSE2.2, FUSE3.2, R13.1, R15.2
unnamed: SRV3.1, WA1.3
unnamed: R23.1, WA1.5
unnamed: SRV4.1, WA1.4
unnamed: R25.1, R26.1, T7.2 (B)
unnamed: R27.1, R28.1, T8.2 (B)
unnamed: R24.2, WA1.6
unnamed: R29.2, T8.3 (C), WB1.6
unnamed: OK3.3 (E), R27.2
unnamed: OK4.3 (E), R25.2
unnamed: R30.2, T7.3 (C), WB1.5
unnamed: R29.1, R30.1, WA1.1
PE: DC-DC.3, L5V.K (C), R19.2, R21.2, SRV1.3, SRV2.3, T1.1 (E), T2.1 (E), T3.1 (E), T4.1 (E), VCC+.2, WB.2

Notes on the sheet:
rst
3v3
Wemos D1 mini
gnd
USB
E. Postma

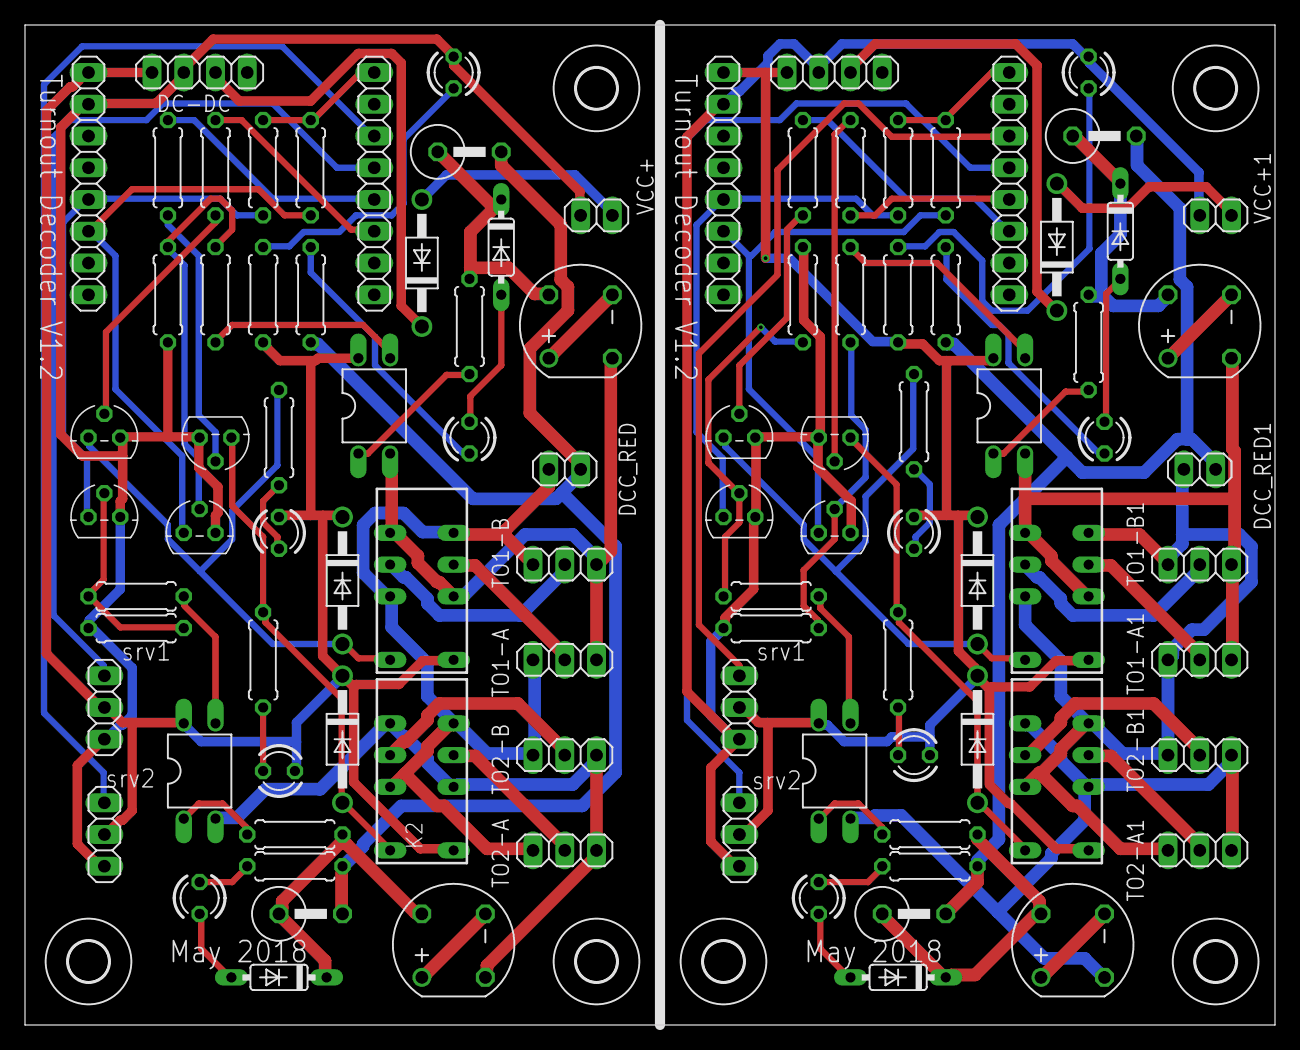
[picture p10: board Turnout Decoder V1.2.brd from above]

Board: 2 copper layers, 100.0 x 80.0 mm, 102 parts (0 on the bottom side), 80 nets.

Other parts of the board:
U$1, U$2, U$3, U$4, U$5, U$6: 3,2

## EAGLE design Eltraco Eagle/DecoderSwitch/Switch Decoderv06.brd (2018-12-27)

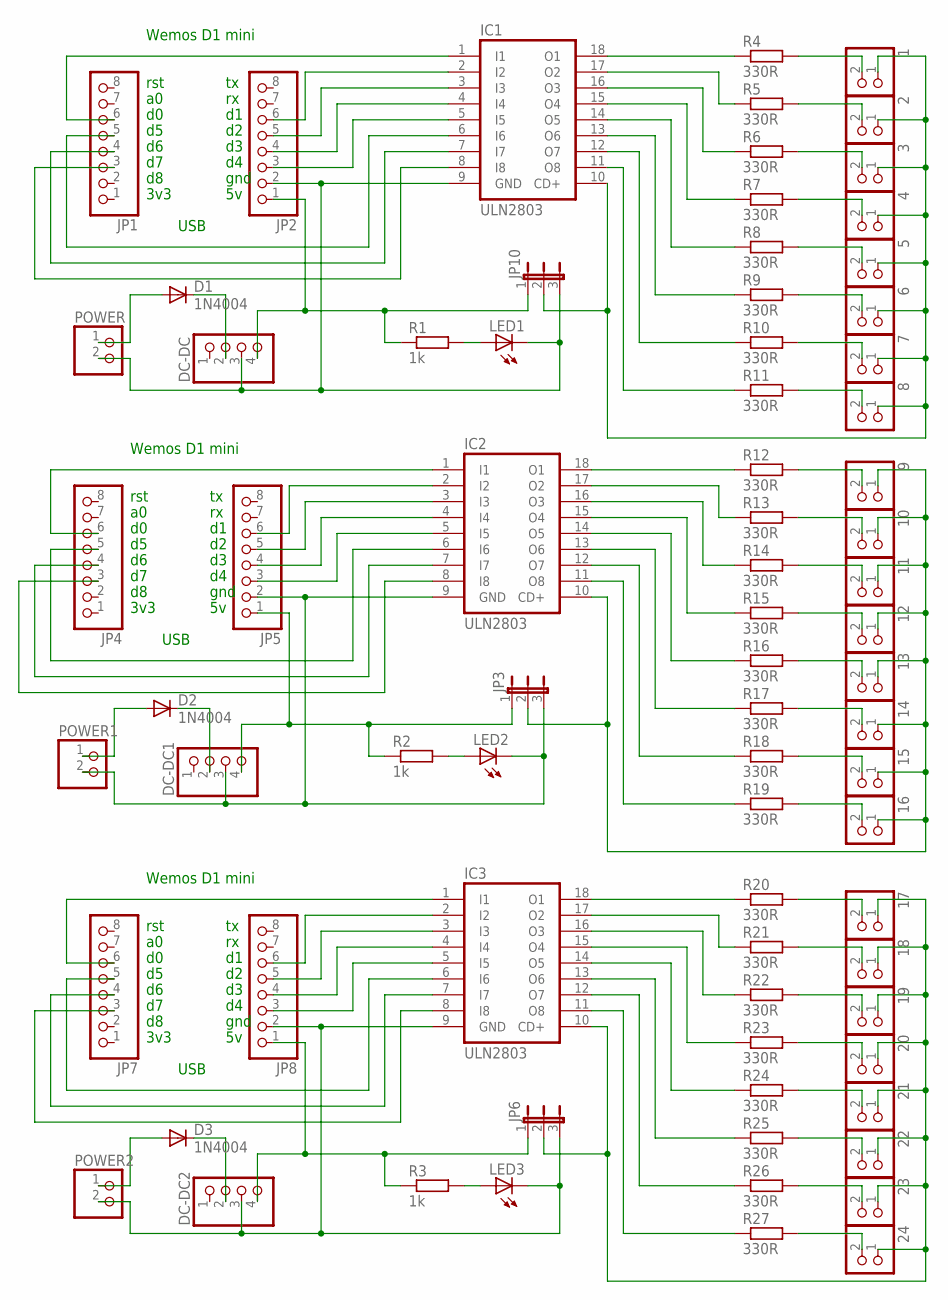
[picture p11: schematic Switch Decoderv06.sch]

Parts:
1, 2, 3, 4, 5, 6, 7, 8, 9, 10, 11, 12, 13, 14, 15, 16, 17, 18, 19, 20, 21, 22, 23, 24: PINHD-1X2; 1X02
D1, D2, D3: 1N4004; DO41-10
DC-DC, DC-DC1, DC-DC2: PINHD-1X4; 1X04
IC1, IC2, IC3: ULN2803; DIL18
JP1, JP2, JP4, JP5, JP7, JP8: PINHD-1X8; 1X08
JP3, JP6, JP10: JP2E; JP2
LED1, LED2, LED3: LED3MM
POWER, POWER1, POWER2: PINHD-1X2; 1X02
R1, R2, R3: 1k; 0309/10
R4, R5, R6, R7, R8, R9, R10, R11, R12, R13, R14, R15, R16, R17, R18, R19, R20, R21, R22, R23, R24, R25, R26, R27: 330R; 0207/7

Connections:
unnamed: DC-DC.3, IC1.9 (GND), JP2.2, JP10.3, LED1.K (C), POWER.2
unnamed: IC1.1 (I1), JP1.6
unnamed: IC1.7 (I7), JP1.4
unnamed: D1.C, DC-DC.2
unnamed: IC1.6 (I6), JP1.5
unnamed: LED1.A, R1.2
unnamed: IC1.3 (I3), JP2.5
unnamed: 1.1, 2.1, 3.1, 4.1, 5.1, 6.1, 7.1, 8.1, IC1.10 (CD+), JP10.2
unnamed: IC1.5 (I5), JP2.3
unnamed: IC1.2 (I2), JP2.6
unnamed: IC1.8 (I8), JP1.3
unnamed: IC1.18 (O1), R4.1
unnamed: IC1.4 (I4), JP2.4
unnamed: IC2.1 (I1), JP4.6
unnamed: 1.2, R4.2
unnamed: 9.1, 10.1, 11.1, 12.1, 13.1, 14.1, 15.1, 16.1, IC2.10 (CD+), JP3.2
unnamed: IC1.17 (O2), R5.1
unnamed: 2.2, R5.2
unnamed: 3.2, R6.2
unnamed: IC1.16 (O3), R6.1
unnamed: IC1.15 (O4), R7.1
unnamed: 4.2, R7.2
unnamed: 5.2, R8.2
unnamed: IC1.14 (O5), R8.1
unnamed: IC1.13 (O6), R9.1
unnamed: 6.2, R9.2
unnamed: 7.2, R10.2
unnamed: IC1.12 (O7), R10.1
unnamed: 8.2, R11.2
unnamed: LED2.A, R2.2
unnamed: IC2.2 (I2), JP5.6
unnamed: IC2.3 (I3), JP5.5
unnamed: IC2.4 (I4), JP5.4
unnamed: D2.A, POWER1.1
unnamed: D2.C, DC-DC1.2
unnamed: IC2.5 (I5), JP5.3
unnamed: IC2.6 (I6), JP4.5
unnamed: IC2.7 (I7), JP4.4
unnamed: IC2.8 (I8), JP4.3
unnamed: IC3.18 (O1), R20.1
unnamed: DC-DC1.3, IC2.9 (GND), JP3.3, JP5.2, LED2.K (C), POWER1.2
unnamed: IC1.11 (O8), R11.1
unnamed: IC2.11 (O8), R19.1
unnamed: IC2.18 (O1), R12.1
unnamed: IC2.17 (O2), R13.1
unnamed: 9.2, R12.2
unnamed: D1.A, POWER.1
unnamed: 10.2, R13.2
unnamed: IC2.16 (O3), R14.1
unnamed: IC2.15 (O4), R15.1
unnamed: 11.2, R14.2
unnamed: 12.2, R15.2
unnamed: IC2.14 (O5), R16.1
unnamed: IC2.13 (O6), R17.1
unnamed: 13.2, R16.2
unnamed: 14.2, R17.2
unnamed: IC2.12 (O7), R18.1
unnamed: 15.2, R18.2
unnamed: IC3.1 (I1), JP7.6
unnamed: LED3.A, R3.2
unnamed: IC3.2 (I2), JP8.6
unnamed: IC3.3 (I3), JP8.5
unnamed: IC3.4 (I4), JP8.4
unnamed: D3.A, POWER2.1
unnamed: D3.C, DC-DC2.2
unnamed: IC3.5 (I5), JP8.3
unnamed: IC3.6 (I6), JP7.5
unnamed: IC3.7 (I7), JP7.4
unnamed: IC3.8 (I8), JP7.3
unnamed: 17.1, 18.1, 19.1, 20.1, 21.1, 22.1, 23.1, 24.1, IC3.10 (CD+), JP6.2
unnamed: DC-DC2.3, IC3.9 (GND), JP6.3, JP8.2, LED3.K (C), POWER2.2
unnamed: 16.2, R19.2
unnamed: IC3.11 (O8), R27.1
unnamed: DC-DC.4, JP2.1, JP10.1, R1.1
unnamed: IC3.17 (O2), R21.1
unnamed: DC-DC1.4, JP3.1, JP5.1, R2.1
unnamed: DC-DC2.4, JP6.1, JP8.1, R3.1
unnamed: IC3.16 (O3), R22.1
unnamed: IC3.15 (O4), R23.1
unnamed: 17.2, R20.2
unnamed: IC3.14 (O5), R24.1
unnamed: IC3.13 (O6), R25.1
unnamed: 18.2, R21.2
unnamed: 19.2, R22.2
unnamed: IC3.12 (O7), R26.1
unnamed: 20.2, R23.2
unnamed: 21.2, R24.2
unnamed: 22.2, R25.2
unnamed: 23.2, R26.2
unnamed: 24.2, R27.2

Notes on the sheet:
rst
3v3
Wemos D1 mini
gnd
USB

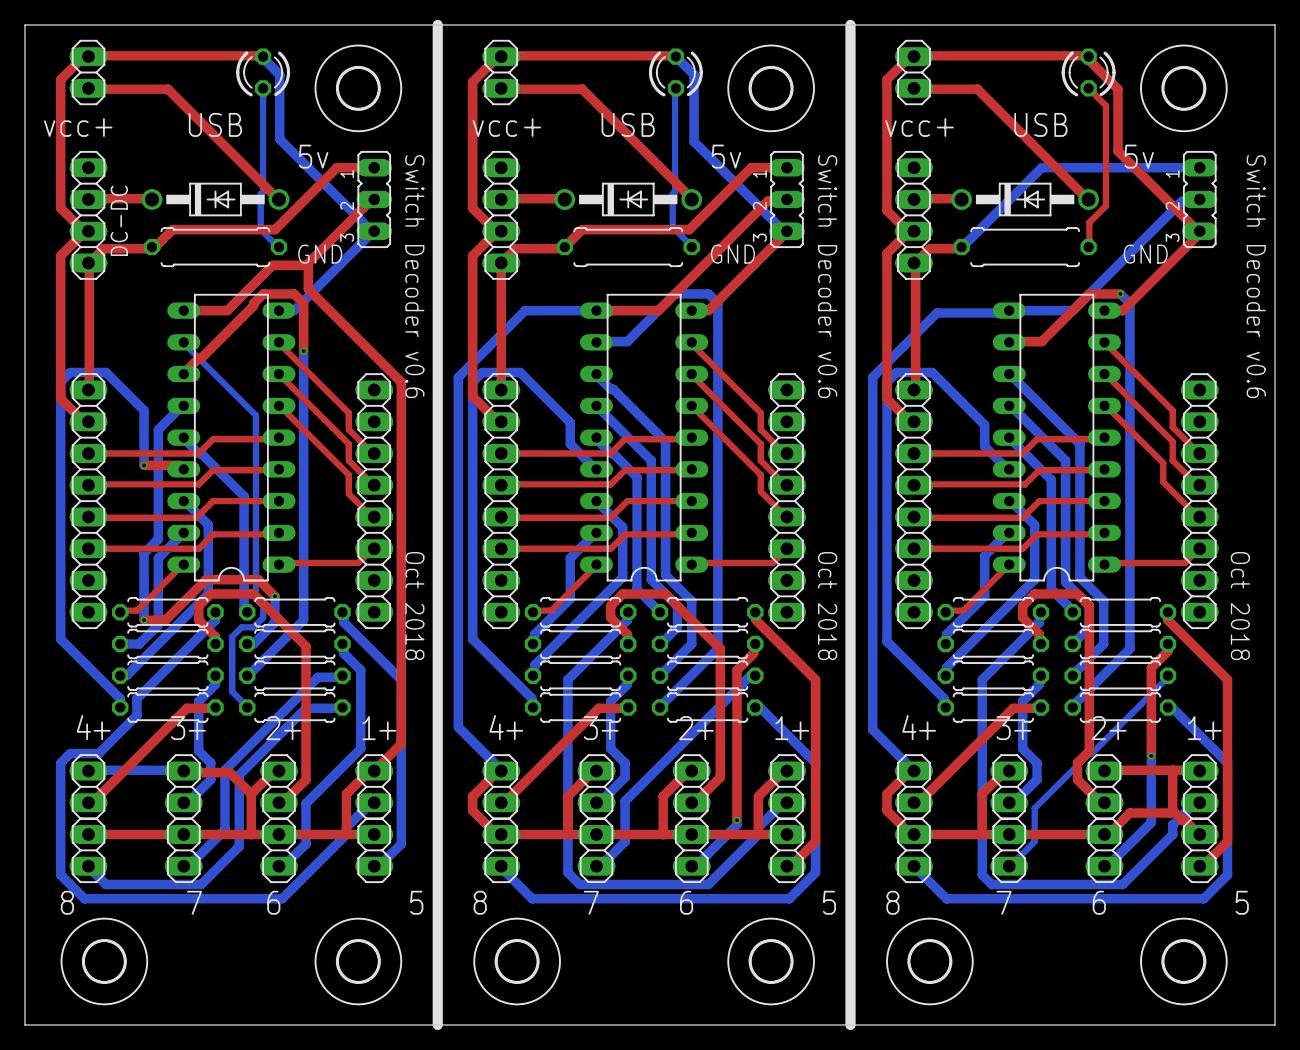
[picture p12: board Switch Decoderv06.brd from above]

Board: 2 copper layers, 100.0 x 80.0 mm, 84 parts (0 on the bottom side), 90 nets.

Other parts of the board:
U$1, U$2, U$3, U$4, U$5, U$6, U$7, U$8, U$9: 3,2

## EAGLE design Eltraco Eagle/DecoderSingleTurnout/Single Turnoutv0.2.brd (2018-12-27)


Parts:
B1, B2: RECTIFIER-RB1A; RB1A
D1, D2, D3, D8: 1N4004; DO41-10
D4, D7: 1N4148DO35-7; DO35-7
DC-DC, DC-DC1: PINHD-1X4; 1X04
DC_RD, DC_RD1: PINHD-1X2; 1X02
FUSE, FUSE1: PFRA050; 0414V
HI, HI1: PINHD-1X6; 1X06
JP1, JP2, JP3, JP4, JP5, JP6, JP7, JP8: PINHD-1X3; 1X03
K1, K2: NA
L5V, L5V1: LED3MM
LO, LO1: PINHD-1X6; 1X06
LREL, LREL1: LED3MM
LSHORT, LSHORT1: LED3MM
OK1, OK2: PC814; DIL04
R1, R2, R5, R26: 330R; 0207/7
R3, R19: 10k; 0207/7
R6, R8: 33R; 0207/7
R7, R11: 2k2; 0207/7
R9, R17: 1k; 0207/7
R10, R20: 3k3; 0207/7
R18, R21: 22k; 0207/7
RN1, RN3: 330R; SIL8
RN2, RN4: 10k; SIL5
SRV, SRV1: PINHD-1X3; 1X03
T1, T2, T3, T4: BC547; TO92
TO-A, TO-A1: PINHD-1X3; 1X03
TO-B, TO-B1: PINHD-1X3; 1X03
VCC+, VCC+1: PINHD-1X2; 1X02
WA, WA1: PINHD-1X8; 1X08
WB, WB1: PINHD-1X8; 1X08

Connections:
+5V/1: D3.C, DC-DC.4, HI.4, JP1.2, JP2.2, JP3.2, JP4.2, K1.1 (+), LREL.A, OK2.4 (C), R1.1, SRV.2, WB.1
+5V/2: D2.C, DC-DC1.4, HI1.4, JP5.2, JP6.2, JP7.2, JP8.2, K2.1 (+), LREL1.A, OK1.4 (C), R26.1, SRV1.2, WB1.1
GND1: DC-DC.3, HI.3, JP1.3, JP2.3, JP3.3, JP4.3, L5V.K (C), LO.3, R21.2, SRV.3, T1.1 (E), T4.1 (E), VCC+.2, WB.2
GND2: DC-DC1.3, HI1.3, JP5.3, JP6.3, JP7.3, JP8.3, L5V1.K (C), LO1.3, R18.2, SRV1.3, T2.1 (E), T3.1 (E), VCC+1.2, WB1.2
unnamed: LO.4, R3.2, RN2.1, WA.1
unnamed: LO.6, RN1.2
unnamed: DC_RD.1, FUSE.2, R11.1
unnamed: D1.A, VCC+.1
unnamed: R3.1, T4.3 (C), WB.6
unnamed: LREL1.K (C), R5.2
unnamed: OK1.1 (AC1), R6.2
unnamed: LSHORT1.A, R7.2
unnamed: D4.A, LSHORT1.K (C)
unnamed: D2.A, K2.12 (-), R5.1, T2.3 (C)
unnamed: R9.1, T2.2 (B)
unnamed: LREL.K (C), R2.2
unnamed: B1.+, B1.-
unnamed: B2.AC2, K1.3 (O), K1.8 (S), OK2.2 (AC2), TO-A.1, TO-B.1
unnamed: K2.4, TO-A1.2
unnamed: DC_RD.2, K1.5 (S), K1.10 (O), TO-A.3, TO-B.3
unnamed: OK2.3 (E), R20.2
unnamed: K2.9, TO-B1.2
unnamed: B1.AC2, K2.3 (O), K2.8 (S), OK1.2 (AC2), TO-A1.1, TO-B1.1
unnamed: B1.AC1, D4.C, FUSE1.1, R6.1
unnamed: OK2.1 (AC1), R8.2
unnamed: DC_RD1.2, K2.5 (S), K2.10 (O), TO-A1.3, TO-B1.3
unnamed: B2.AC1, D7.C, FUSE.1, R8.1
unnamed: LO.5, RN1.4 (2)
unnamed: HI.2, JP3.1
unnamed: K1.4, TO-A.2
unnamed: DC_RD1.1, FUSE1.2, R7.1
unnamed: R20.1, R21.1, T4.2 (B)
unnamed: R17.2, WA.6
unnamed: HI.5, JP2.1
unnamed: SRV.1, WA.4
unnamed: K1.9, TO-B.2
unnamed: SRV1.1, WA1.4
unnamed: R10.1, R18.1, T3.2 (B)
unnamed: LSHORT.A, R11.2
unnamed: HI.6, JP1.1
unnamed: RN1.3 (1), RN2.3, WB.4
unnamed: RN1.1, RN2.2, WB.5
unnamed: HI1.2, JP7.1
unnamed: HI1.5, JP6.1
unnamed: D7.A, LSHORT.K (C)
unnamed: B2.+, B2.-
unnamed: HI1.6, JP5.1
unnamed: RN1.5 (1), RN2.4, WB.3
unnamed: RN1.7 (1), RN2.5, WA.5
unnamed: L5V.A, R1.2
unnamed: RN3.5 (1), RN4.4, WB1.3
unnamed: LO1.4, R19.2, RN4.1, WA1.1
unnamed: R17.1, T1.2 (B)
unnamed: D3.A, K1.12 (-), R2.1, T1.3 (C)
unnamed: RN3.7 (1), RN4.5, WA1.5
unnamed: HI1.1, JP8.1
unnamed: LO.2, RN1.6 (2)
unnamed: RN3.3 (1), RN4.3, WB1.4
unnamed: RN3.1, RN4.2, WB1.5
unnamed: LO.1, RN1.8 (2)
unnamed: LO1.6, RN3.2
unnamed: D1.C, DC-DC.2
unnamed: LO1.5, RN3.4 (2)
unnamed: LO1.2, RN3.6 (2)
unnamed: HI.1, JP4.1
unnamed: R9.2, WA1.6
unnamed: OK1.3 (E), R10.2
unnamed: L5V1.A, R26.2
unnamed: R19.1, T3.3 (C), WB1.6
unnamed: LO1.1, RN3.8 (2)
unnamed: D8.A, VCC+1.1
unnamed: D8.C, DC-DC1.2

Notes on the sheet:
rst
3v3
Wemos D1 mini
gnd
USB


Board: 2 copper layers, 100.0 x 80.0 mm, 78 parts (0 on the bottom side), 72 nets.

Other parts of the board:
U$1, U$2, U$4, U$5, U$6, U$9: 3,2

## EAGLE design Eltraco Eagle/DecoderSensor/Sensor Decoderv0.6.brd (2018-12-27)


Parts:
D1, D2: 1N4004; DO41-10
DC-DC, DC-DC1: PINHD-1X4; 1X04
HIGH1, HIGH2, HIGH3, HIGH4: PINHD-1X6; 1X06
JP1, JP2, JP3, JP4: PINHD-1X8; 1X08
JP5, JP6: PINHD-1X10; 1X10
JP7, JP8: PINHD-1X4; 1X04
LED1, LED2: LED3MM
LOW1, LOW2, LOW3, LOW4: PINHD-1X6; 1X06
R1, R2: 330R; 0207/7
R3, R8: 5k1; 0207/7
R4, R5, R6, R7: 10k; 0207/7
RN1, RN3, RN5, RN6: 330R; SIL8
RN2, RN4: 10k; SIL9
SR1, SR2, SR3, SR4, SR5, SR6, SR7, SR8, SR9, SR10, SR11, SR12, SR13, SR14, SR15, SR16, SR17, SR18: PINHD-1X3; 1X03
VCC+, VCC+1: PINHD-1X2; 1X02

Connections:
+3V3: JP1.1, LOW1.3, LOW2.3, R5.1, RN2.1
+5V: DC-DC.4, HIGH1.3, HIGH2.3, JP2.1, JP5.8, JP5.9, JP7.3, R1.1, SR1.2, SR2.2, SR3.2, SR4.2, SR5.2, SR6.2, SR7.2, SR8.2, SR17.2
unnamed: HIGH2.6, JP5.5, SR8.1
unnamed: JP1.6, RN1.1, RN2.2
unnamed: JP1.4, RN2.8, RN3.5 (1)
unnamed: D1.C, DC-DC.2
unnamed: JP1.5, RN2.7, RN3.3 (1)
unnamed: LED1.A, R1.2
unnamed: JP2.5, RN1.5 (1), RN2.4
unnamed: HIGH2.5, JP5.4, SR7.1
unnamed: JP2.3, RN2.6, RN3.1
unnamed: JP2.6, RN1.3 (1), RN2.3
unnamed: JP1.3, RN2.9, RN3.7 (1)
unnamed: LOW1.1, RN1.2
unnamed: JP2.4, RN1.7 (1), RN2.5
unnamed: HIGH1.5, JP7.2, SR3.1
unnamed: HIGH1.1, SR1.1
unnamed: HIGH1.6, JP5.1, SR4.1
unnamed: HIGH1.2, JP7.1, SR2.1
unnamed: HIGH2.2, JP5.3, SR6.1
unnamed: HIGH2.1, JP5.2, SR5.1
unnamed: JP3.6, RN4.2, RN5.1
unnamed: LED2.A, R2.2
unnamed: JP4.6, RN4.3, RN5.3 (1)
unnamed: JP4.5, RN4.4, RN5.5 (1)
unnamed: JP4.4, RN4.5, RN5.7 (1)
unnamed: D2.A, VCC+1.1
unnamed: D2.C, DC-DC1.2
unnamed: JP4.3, RN4.6, RN6.1
unnamed: JP3.5, RN4.7, RN6.3 (1)
unnamed: JP3.4, RN4.8, RN6.5 (1)
unnamed: JP3.3, RN4.9, RN6.7 (1)
unnamed: LOW3.1, RN5.2
unnamed: LOW3.2, RN5.4 (2)
unnamed: LOW3.5, RN5.6 (2)
unnamed: LOW3.6, RN5.8 (2)
unnamed: LOW4.1, RN6.2
unnamed: LOW4.2, RN6.4 (2)
unnamed: LOW4.5, RN6.6 (2)
unnamed: LOW4.6, RN6.8 (2)
unnamed: HIGH4.6, JP6.5, SR16.1
unnamed: HIGH4.5, JP6.4, SR15.1
unnamed: DC-DC1.3, HIGH3.4, HIGH4.4, JP4.2, JP6.10, JP8.4, LED2.K (C), LOW3.4, LOW4.4, R4.2, SR9.3, SR10.3, SR11.3, SR12.3, SR13.3, SR14.3, SR15.3, SR16.3, SR18.3, VCC+1.2
unnamed: JP3.8, JP6.7
unnamed: JP1.8, JP5.7
unnamed: LOW1.2, RN1.4 (2)
unnamed: LOW1.5, RN1.6 (2)
unnamed: LOW1.6, RN1.8 (2)
unnamed: D1.A, VCC+.1
unnamed: LOW2.1, RN3.2
unnamed: LOW2.2, RN3.4 (2)
unnamed: LOW2.5, RN3.6 (2)
unnamed: LOW2.6, RN3.8 (2)
unnamed: DC-DC1.4, HIGH3.3, HIGH4.3, JP4.1, JP6.8, JP6.9, JP8.3, R2.1, SR9.2, SR10.2, SR11.2, SR12.2, SR13.2, SR14.2, SR15.2, SR16.2, SR18.2
unnamed: HIGH3.1, SR9.1
unnamed: JP3.1, LOW3.3, LOW4.3, R6.1, RN4.1
unnamed: JP1.7, R5.2, R7.2, R8.2
unnamed: JP3.7, R3.1, R4.1, R6.2
unnamed: R3.2, SR18.1
unnamed: HIGH3.2, JP8.1, SR10.1
unnamed: R8.1, SR17.1
unnamed: HIGH3.5, JP8.2, SR11.1
unnamed: HIGH3.6, JP6.1, SR12.1
unnamed: HIGH4.2, JP6.3, SR14.1
unnamed: HIGH4.1, JP6.2, SR13.1
PE: DC-DC.3, HIGH1.4, HIGH2.4, JP2.2, JP5.10, JP7.4, LED1.K (C), LOW1.4, LOW2.4, R7.1, SR1.3, SR2.3, SR3.3, SR4.3, SR5.3, SR6.3, SR7.3, SR8.3, SR17.3, VCC+.2

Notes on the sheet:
rst
3v3
Wemos D1 mini
gnd
USB
E. Postma


Board: 2 copper layers, 100.0 x 80.0 mm, 64 parts (0 on the bottom side), 66 nets.

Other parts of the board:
U$1, U$2, U$3, U$4, U$5, U$6, U$7, U$8: 3,2

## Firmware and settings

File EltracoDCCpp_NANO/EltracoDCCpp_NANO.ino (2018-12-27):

/**********************************************************************
This software is adapted to run on Arduino Nano with Arduino Nano motorshield.

The functionality has been reduced to just providing driving current.
One could say it acts like a DCC++ "booster"

The next enhancement would be to make the operation wireless via WiFi and control it via MQTT.

Maybe someone out there could port it to ESP8266/Wemos?

eporocrail

oktober 2017


/********************************************
  DCC++ BASE STATION
  COPYRIGHT (c) 2013-2016 Gregg E. Berman

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
**********************************************************************/
/**********************************************************************

  DCC++ BASE STATION is a C++ program written for the Arduino Uno and Arduino Mega
  using the Arduino IDE 1.6.6.

  It allows a standard Arduino Uno or Mega with an Arduino Motor Shield (as well as others)
  to be used as a fully-functioning digital command and control (DCC) base station
  for controlling model train layouts that conform to current National Model
  Railroad Association (NMRA) DCC standards.

  This version of DCC++ BASE STATION supports:

    2-byte and 4-byte locomotive addressing
    Simultaneous control of multiple locomotives
    128-step speed throttling
    Cab functions F0-F28
    Activate/de-activate accessory functions using 512 addresses, each with 4 sub-addresses
      - includes optional functionailty to monitor and store of the direction of any connected turnouts
    Programming on the Main Operations Track
      - write configuration variable bytes
      - set/clear specific configuration variable bits
    Programming on the Programming Track
      - write configuration variable bytes
      - set/clear specific configuration variable bits
      - read configuration variable bytes

  DCC++ BASE STATION is controlled with simple text commands received via
  the Arduino's serial interface.  Users can type these commands directly
  into the Arduino IDE Serial Monitor, or can send such commands from another
  device or computer program.

  When compiled for the Arduino Mega, an Ethernet Shield can be used for network
  communications instead of using serial communications.

  DCC++ CONTROLLER, available separately under a similar open-source
  license, is a Java program written using the Processing library and Processing IDE
  that provides a complete and configurable graphic interface to control model train layouts
  via the DCC++ BASE STATION.

  With the exception of a standard 15V power supply that can be purchased in
  any electronics store, no additional hardware is required.

  Neither DCC++ BASE STATION nor DCC++ CONTROLLER use any known proprietary or
  commercial hardware, software, interfaces, specifications, or methods related
  to the control of model trains using NMRA DCC standards.  Both programs are wholly
  original, developed by the author, and are not derived from any known commercial,
  free, or open-source model railroad control packages by any other parties.

  However, DCC++ BASE STATION and DCC++ CONTROLLER do heavily rely on the IDEs and
  embedded libraries associated with Arduino and Processing.  Tremendous thanks to those
  responsible for these terrific open-source initiatives that enable programs like
  DCC++ to be developed and distributed in the same fashion.

  REFERENCES:

  NMRA DCC Standards:          http://www.nmra.org/index-nmra-standards-and-recommended-practices
  Arduino:                     http://www.arduino.cc/
  Processing:                  http://processing.org/
  GNU General Public License:  http://opensource.org/licenses/GPL-3.0

  BRIEF NOTES ON THE THEORY AND OPERATION OF DCC++ BASE STATION:

  DCC++ BASE STATION for the Uno configures the OC0B interrupt pin associated with Timer 0,
  and the OC1B interupt pin associated with Timer 1, to generate separate 0-5V
  unipolar signals that each properly encode zero and one bits conforming with
  DCC timing standards.  When compiled for the Mega, DCC++ BASE STATION uses OC3B instead of OC0B.

  Series of DCC bit streams are bundled into Packets that each form the basis of
  a standard DCC instruction.  Packets are stored in Packet Registers that contain
  methods for updating and queuing according to text commands sent by the user
  (or another program) over the serial interface.  There is one set of registers that controls
  the main operations track and one that controls the programming track.

  For the main operations track, packets to store cab throttle settings are stored in
  registers numbered 1 through MAX_MAIN_REGISTERS (as defined in DCCpp_Uno.h).
  It is generally considered good practice to continuously send throttle control packets
  to every cab so that if an engine should momentarily lose electrical connectivity with the tracks,
  it will very quickly receive another throttle control signal as soon as connectivity is
  restored (such as when a trin passes over  rough portion of track or the frog of a turnout).

  DCC++ Base Station therefore sequentially loops through each main operations track packet regsiter
  that has been loaded with a throttle control setting for a given cab.  For each register, it
  transmits the appropriate DCC packet bits to the track, then moves onto the next register
  without any pausing to ensure continuous bi-polar power is being provided to the tracks.
  Updates to the throttle setting stored in any given packet register are done in a double-buffered
  fashion and the sequencer is pointed to that register immediately after being changes so that updated DCC bits
  can be transmitted to the appropriate cab without delay or any interruption in the bi-polar power signal.
  The cabs identified in each stored throttle setting should be unique across registers.  If two registers
  contain throttle setting for the same cab, the throttle in the engine will oscillate between the two,
  which is probably not a desireable outcome.

  For both the main operations track and the programming track there is also a special packet register with id=0
  that is used to store all other DCC packets that do not require continious transmittal to the tracks.
  This includes DCC packets to control decoder functions, set accessory decoders, and read and write Configuration Variables.
  It is common practice that transmittal of these one-time packets is usually repeated a few times to ensure
  proper receipt by the receiving decoder.  DCC decoders are designed to listen for repeats of the same packet
  and provided there are no other packets received in between the repeats, the DCC decoder will not repeat the action itself.
  Some DCC decoders actually require receipt of sequential multiple identical one-time packets as a way of
  verifying proper transmittal before acting on the instructions contained in those packets

  An Arduino Motor Shield (or similar), powered by a standard 15V DC power supply and attached
  on top of the Arduino Uno or Mega, is used to transform the 0-5V DCC logic signals
  produced by the Uno's Timer interrupts into proper 0-15V bi-polar DCC signals.

  This is accomplished on the Uno by using one small jumper wire to connect the Uno's OC1B output (pin 10)
  to the Motor Shield's DIRECTION A input (pin 12), and another small jumper wire to connect
  the Uno's OC0B output (pin 5) to the Motor Shield's DIRECTION B input (pin 13).

  For the Mega, the OC1B output is produced directly on pin 12, so no jumper is needed to connect to the
  Motor Shield's DIRECTION A input.  However, one small jumper wire is needed to connect the Mega's OC3B output (pin 2)
  to the Motor Shield's DIRECTION B input (pin 13).

  Other Motor Shields may require different sets of jumper or configurations (see Config.h and DCCpp_Uno.h for details).

  When configured as such, the CHANNEL A and CHANNEL B outputs of the Motor Shield may be
  connected directly to the tracks.  This software assumes CHANNEL A is connected
  to the Main Operations Track, and CHANNEL B is connected to the Programming Track.

  DCC++ BASE STATION in split into multiple modules, each with its own header file:

  DCCpp_Uno:        declares required global objects and contains initial Arduino setup()
                    and Arduino loop() functions, as well as interrput code for OC0B and OC1B.
                    Also includes declarations of optional array of Turn-Outs and optional array of Sensors

  SerialCommand:    contains methods to read and interpret text commands from the serial line,
                    process those instructions, and, if necessary call appropriate Packet RegisterList methods
                    to update either the Main Track or Programming Track Packet Registers

  PacketRegister:   contains methods to load, store, and update Packet Registers with DCC instructions

  CurrentMonitor:   contains methods to separately monitor and report the current drawn from CHANNEL A and
                    CHANNEL B of the Arduino Motor Shield's, and shut down power if a short-circuit overload
                    is detected

  Accessories:      contains methods to operate and store the status of any optionally-defined turnouts controlled
                    by a DCC stationary accessory decoder.

  Sensor:           contains methods to monitor and report on the status of optionally-defined infrared
                    sensors embedded in the Main Track and connected to various pins on the Arudino Uno

  Outputs:          contains methods to configure one or more Arduino pins as an output for your own custom use

  EEStore:          contains methods to store, update, and load various DCC settings and status
                    (e.g. the states of all defined turnouts) in the EEPROM for recall after power-up

  DCC++ BASE STATION is configured through the Config.h file that contains all user-definable parameters

**********************************************************************/

// BEGIN BY INCLUDING THE HEADER FILES FOR EACH MODULE

#include "DCCpp_Uno.h"
#include "PacketRegister.h"
#include "CurrentMonitor.h"
#include "SerialCommand.h"
#include "Config.h"

void showConfiguration();

// SET UP COMMUNICATIONS INTERFACE - FOR STANDARD SERIAL, NOTHING NEEDS TO BE DONE


// NEXT DECLARE GLOBAL OBJECTS TO PROCESS AND STORE DCC PACKETS AND MONITOR TRACK CURRENTS.
// NOTE REGISTER LISTS MUST BE DECLARED WITH "VOLATILE" QUALIFIER TO ENSURE THEY ARE PROPERLY UPDATED BY INTERRUPT ROUTINES

volatile RegisterList mainRegs(MAX_MAIN_REGISTERS);    // create list of registers for MAX_MAIN_REGISTER Main Track Packets
volatile RegisterList progRegs(2);                     // create a shorter list of only two registers for Program Track Packets

CurrentMonitor mainMonitor(CURRENT_MONITOR_PIN_MAIN, "<p2>"); // create monitor for current on Main Track
CurrentMonitor progMonitor(CURRENT_MONITOR_PIN_PROG, "<p3>"); // create monitor for current on Program Track

///////////////////////////////////////////////////////////////////////////////
// MAIN ARDUINO LOOP
///////////////////////////////////////////////////////////////////////////////

void loop() {

  SerialCommand::process();              // check for, and process, and new serial commands

  if (CurrentMonitor::checkTime()) {    // if sufficient time has elapsed since last update, check current draw on Main and Program Tracks
    mainMonitor.check();
    progMonitor.check();
  }


} // loop

///////////////////////////////////////////////////////////////////////////////
// INITIAL SETUP
///////////////////////////////////////////////////////////////////////////////

void setup() {

  Serial.begin(115200);            // configure serial interface
  Serial.flush();

  pinMode(A5, INPUT);                                      // if pin A5 is grounded upon start-up, print system configuration and halt
  digitalWrite(A5, HIGH);
  if (!digitalRead(A5))
    showConfiguration();

  Serial.println();
  Serial.println();
  Serial.print("< iDCC++ BASE STATION FOR ARDUINO ");      // Print Status to Serial Line regardless of COMM_TYPE setting so you can open Serial Monitor and check configurtion
  Serial.print(ARDUINO_TYPE);
  Serial.print(" - Motor shield: ");
  Serial.print(MOTOR_SHIELD_NAME);
  Serial.print(" >");
  Serial.println();
  Serial.print("< Firmware version: ");
  Serial.print(VERSION);
  Serial.print(" - sketch compiled on: ");
  Serial.print(__DATE__);
  Serial.print(" ");
  Serial.print(__TIME__);
  Serial.print(" >");
  Serial.println();

  SerialCommand::init(&mainRegs, &progRegs, &mainMonitor);   // create structure to read and parse commands from serial line

  Serial.print("< Communication via: ");

#if COMM_TYPE == 0
  Serial.print("USB - SERIAL >");
#endif
  Serial.println();

  // CONFIGURE TIMER_1 TO OUTPUT 50% DUTY CYCLE DCC SIGNALS ON OC1B INTERRUPT PINS

  // Direction Pin for Motor Shield Channel A - MAIN OPERATIONS TRACK
  // Controlled by Arduino 16-bit TIMER 1 / OC1B Interrupt Pin
  // Values for 16-bit OCR1A and OCR1B registers calibrated for 1:1 prescale at 16 MHz clock frequency
  // Resulting waveforms are 200 microseconds for a ZERO bit and 116 microseconds for a ONE bit with exactly 50% duty cycle

#define DCC_ZERO_BIT_TOTAL_DURATION_TIMER1 3199
#define DCC_ZERO_BIT_PULSE_DURATION_TIMER1 1599

#define DCC_ONE_BIT_TOTAL_DURATION_TIMER1 1855
#define DCC_ONE_BIT_PULSE_DURATION_TIMER1 927

  pinMode(DIRECTION_MOTOR_CHANNEL_PIN_A, INPUT);     // ensure this pin is not active! Direction will be controlled by DCC SIGNAL instead (below)
  digitalWrite(DIRECTION_MOTOR_CHANNEL_PIN_A, LOW);

  pinMode(DCC_SIGNAL_PIN_MAIN, OUTPUT);      // THIS ARDUINO OUPUT PIN MUST BE PHYSICALLY CONNECTED TO THE PIN FOR DIRECTION-A OF MOTOR CHANNEL-A

  bitSet(TCCR1A, WGM10);    // set Timer 1 to FAST PWM, with TOP=OCR1A
  bitSet(TCCR1A, WGM11);
  bitSet(TCCR1B, WGM12);
  bitSet(TCCR1B, WGM13);

  bitSet(TCCR1A, COM1B1);   // set Timer 1, OC1B (pin 10/UNO, pin 12/MEGA) to inverting toggle (actual direction is arbitrary)
  bitSet(TCCR1A, COM1B0);

  bitClear(TCCR1B, CS12);   // set Timer 1 prescale=1
  bitClear(TCCR1B, CS11);
  bitSet(TCCR1B, CS10);

  OCR1A = DCC_ONE_BIT_TOTAL_DURATION_TIMER1;
  OCR1B = DCC_ONE_BIT_PULSE_DURATION_TIMER1;

  pinMode(SIGNAL_ENABLE_PIN_MAIN, OUTPUT);  // master enable for motor channel A

  mainRegs.loadPacket(1, RegisterList::idlePacket, 2, 0); // load idle packet into register 1

  bitSet(TIMSK1, OCIE1B);   // enable interrupt vector for Timer 1 Output Compare B Match (OCR1B)

  // CONFIGURE TIMER_0 (NANO) TO OUTPUT 50% DUTY CYCLE DCC SIGNALS ON OC0B (UNO) INTERRUPT PINS


#ifdef ARDUINO_AVR_NANO      // Configuration for UNO
  // Directon Pin for Motor Shield Channel B - PROGRAMMING TRACK
  // Controlled by Arduino 8-bit TIMER 0 / OC0B Interrupt Pin
  // Values for 8-bit OCR0A and OCR0B registers calibrated for 1:64 prescale at 16 MHz clock frequency
  // Resulting waveforms are 200 microseconds for a ZERO bit and 116 microseconds for a ONE bit with as-close-as-possible to 50% duty cycle

#define DCC_ZERO_BIT_TOTAL_DURATION_TIMER0 49
#define DCC_ZERO_BIT_PULSE_DURATION_TIMER0 24

#define DCC_ONE_BIT_TOTAL_DURATION_TIMER0 28
#define DCC_ONE_BIT_PULSE_DURATION_TIMER0 14

  pinMode(DIRECTION_MOTOR_CHANNEL_PIN_B, INPUT);     // ensure this pin is not active! Direction will be controlled by DCC SIGNAL instead (below)
  digitalWrite(DIRECTION_MOTOR_CHANNEL_PIN_B, LOW);

  pinMode(DCC_SIGNAL_PIN_PROG, OUTPUT);     // THIS ARDUINO OUTPUT PIN MUST BE PHYSICALLY CONNECTED TO THE PIN FOR DIRECTION-B OF MOTOR CHANNEL-B

  bitSet(TCCR0A, WGM00);    // set Timer 0 to FAST PWM, with TOP=OCR0A
  bitSet(TCCR0A, WGM01);
  bitSet(TCCR0B, WGM02);

  bitSet(TCCR0A, COM0B1);   // set Timer 0, OC0B (pin 5) to inverting toggle (actual direction is arbitrary)
  bitSet(TCCR0A, COM0B0);

  bitClear(TCCR0B, CS02);   // set Timer 0 prescale=64
  bitSet(TCCR0B, CS01);
  bitSet(TCCR0B, CS00);

  OCR0A = DCC_ONE_BIT_TOTAL_DURATION_TIMER0;
  OCR0B = DCC_ONE_BIT_PULSE_DURATION_TIMER0;

  pinMode(SIGNAL_ENABLE_PIN_PROG, OUTPUT);  // master enable for motor channel B

  progRegs.loadPacket(1, RegisterList::idlePacket, 2, 0); // load idle packet into register 1

  bitSet(TIMSK0, OCIE0B);   // enable interrupt vector for Timer 0 Output Compare B Match (OCR0B)

#endif

} // setup

///////////////////////////////////////////////////////////////////////////////
// DEFINE THE INTERRUPT LOGIC THAT GENERATES THE DCC SIGNAL
///////////////////////////////////////////////////////////////////////////////

// The code below will be called every time an interrupt is triggered on OCNB, where N can be 0 or 1.
// It is designed to read the current bit of the current register packet and
// updates the OCNA and OCNB counters of Timer-N to values that will either produce
// a long (200 microsecond) pulse, or a short (116 microsecond) pulse, which respectively represent
// DCC ZERO and DCC ONE bits.

// These are hardware-driven interrupts that will be called automatically when triggered regardless of what
// DCC++ BASE STATION was otherwise processing.  But once inside the interrupt, all other interrupt routines are temporarily diabled.
// Since a short pulse only lasts for 116 microseconds, and there are TWO separate interrupts
// (one for Main Track Registers and one for the Program Track Registers), the interrupt code must complete
// in much less than 58 microsends, otherwise there would be no time for the rest of the program to run.  Worse, if the logic
// of the interrupt code ever caused it to run longer than 58 microsends, an interrupt trigger would be missed, the OCNA and OCNB
// registers would not be updated, and the net effect would be a DCC signal that keeps sending the same DCC bit repeatedly until the
// interrupt code completes and can be called again.

// A significant portion of this entire program is designed to do as much of the heavy processing of creating a properly-formed
// DCC bit stream upfront, so that the interrupt code below can be as simple and efficient as possible.

// Note that we need to create two very similar copies of the code --- one for the Main Track OC1B interrupt and one for the
// Programming Track OCOB interrupt.  But rather than create a generic function that incurrs additional overhead, we create a macro
// that can be invoked with proper paramters for each interrupt.  This slightly increases the size of the code base by duplicating
// some of the logic for each interrupt, but saves additional time.

// As structured, the interrupt code below completes at an average of just under 6 microseconds with a worse-case of just under 11 microseconds
// when a new register is loaded and the logic needs to switch active register packet pointers.

// THE INTERRUPT CODE MACRO:  R=REGISTER LIST (mainRegs or progRegs), and N=TIMER (0 or 1)

#define DCC_SIGNAL(R,N) \
  if(R.currentBit==R.currentReg->activePacket->nBits){    /* IF no more bits in this DCC Packet */ \
    R.currentBit=0;                                       /*   reset current bit pointer and determine which Register and Packet to process next--- */ \
    if(R.nRepeat>0 && R.currentReg==R.reg){               /*   IF current Register is first Register AND should be repeated */ \
      R.nRepeat--;                                        /*     decrement repeat count; result is this same Packet will be repeated */ \
    } else if(R.nextReg!=NULL){                           /*   ELSE IF another Register has been updated */ \
      R.currentReg=R.nextReg;                             /*     update currentReg to nextReg */ \
      R.nextReg=NULL;                                     /*     reset nextReg to NULL */ \
      R.tempPacket=R.currentReg->activePacket;            /*     flip active and update Packets */ \
      R.currentReg->activePacket=R.currentReg->updatePacket; \
      R.currentReg->updatePacket=R.tempPacket; \
    } else{                                               /*   ELSE simply move to next Register */ \
      if(R.currentReg==R.maxLoadedReg)                    /*     BUT IF this is last Register loaded */ \
        R.currentReg=R.reg;                               /*       first reset currentReg to base Register, THEN */ \
      R.currentReg++;                                     /*     increment current Register (note this logic causes Register[0] to be skipped when simply cycling through all Registers) */ \
    }                                                     /*   END-ELSE */ \
  }                                                       /* END-IF: currentReg, activePacket, and currentBit should now be properly set to point to next DCC bit */ \
  \
  if(R.currentReg->activePacket->buf[R.currentBit/8] & R.bitMask[R.currentBit%8]){     /* IF bit is a ONE */ \
    OCR ## N ## A=DCC_ONE_BIT_TOTAL_DURATION_TIMER ## N;                               /*   set OCRA for timer N to full cycle duration of DCC ONE bit */ \
    OCR ## N ## B=DCC_ONE_BIT_PULSE_DURATION_TIMER ## N;                               /*   set OCRB for timer N to half cycle duration of DCC ONE but */ \
  } else{                                                                              /* ELSE it is a ZERO */ \
    OCR ## N ## A=DCC_ZERO_BIT_TOTAL_DURATION_TIMER ## N;                              /*   set OCRA for timer N to full cycle duration of DCC ZERO bit */ \
    OCR ## N ## B=DCC_ZERO_BIT_PULSE_DURATION_TIMER ## N;                              /*   set OCRB for timer N to half cycle duration of DCC ZERO bit */ \
  }                                                                                    /* END-ELSE */ \
  \
  R.currentBit++;                                         /* point to next bit in current Packet */

///////////////////////////////////////////////////////////////////////////////

// NOW USE THE ABOVE MACRO TO CREATE THE CODE FOR EACH INTERRUPT
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

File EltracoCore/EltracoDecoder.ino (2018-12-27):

#include <ESP8266WiFi.h>
#include <ESP8266WebServer.h>
#include <EmbAJAX.h>
#include <EEPROM.h>
#include <Servo.h>
#include <stdlib.h>
#include <PubSubClient.h>
#include <FS.h>
#include <ESP8266FtpServer.h>
#include <Wire.h>
#include <ArduinoOTA.h>

#include "Defaults.h"

WiFiClient espClient;
ESP8266WebServer server(80);
EmbAJAXOutputDriverESP8266 driver(&server);
Servo servoMotor[2];
PubSubClient client(espClient);
FtpServer ftpSrv;   //set #define FTP_DEBUG in ESP8266FtpServer.h to see ftp verbose on serial


/////////////////////////////////////////////// General /////////////////////////////////////////////
EmbAJAXTextInput<BUFLENTRIP> triplet0("triplet0"); EmbAJAXMutableSpan triplet0_d("triplet0_d"); char triplet0_buf[BUFLENTRIP];
EmbAJAXTextInput<BUFLENTRIP> triplet1("triplet1"); EmbAJAXMutableSpan triplet1_d("triplet1_d"); char triplet1_buf[BUFLENTRIP];
EmbAJAXTextInput<BUFLENTRIP> triplet2("triplet2"); EmbAJAXMutableSpan triplet2_d("triplet2_d"); char triplet2_buf[BUFLENTRIP];
EmbAJAXTextInput<BUFLENTRIP> triplet3("triplet3"); EmbAJAXMutableSpan triplet3_d("triplet3_d"); char triplet3_buf[BUFLENTRIP];
EmbAJAXTextInput<BUFLENTRIP> triplet4("triplet4"); EmbAJAXMutableSpan triplet4_d("triplet4_d"); char triplet4_buf[BUFLENTRIP];
EmbAJAXTextInput<BUFLENTRIP> triplet5("triplet5"); EmbAJAXMutableSpan triplet5_d("triplet5_d"); char triplet5_buf[BUFLENTRIP];

EmbAJAXTextInput<BUFLENSSID> ssid("ssid"); EmbAJAXMutableSpan ssid_d("ssid_d"); char ssid_buf[BUFLENSSID];
EmbAJAXTextInput<BUFLENPWD> pwd("pwd"); EmbAJAXMutableSpan pwd_d("pwd_d"); char pwd_buf[BUFLENPWD];

const char* type_opts[] = {"single turnout", "double turnout", "sensor", "switch"};

EmbAJAXOptionSelect<5> type("type", type_opts); EmbAJAXMutableSpan type_d("type_d");

const char* debug_opts[] = {"no", "yes"}; EmbAJAXOptionSelect<2> debug("debug", debug_opts); EmbAJAXMutableSpan debug_d("debug_d");
const char* wifiReset_opts[] = {"no", "yes"}; EmbAJAXOptionSelect<2> wifiReset("wifiReset", wifiReset_opts); EmbAJAXMutableSpan wifiReset_d("wifiReset_d");
const char* initial_opts[] = {"no", "yes"}; EmbAJAXOptionSelect<2> initial("initial", initial_opts); EmbAJAXMutableSpan initial_d("initial_d");

///////////////////////////////////////////// servo1 //////////////////////////////////////////
EmbAJAXSlider sliderAngleB1("sliderAngleB1", 0, 180, 90); EmbAJAXMutableSpan sliderAngleB1_d("sliderAngleB1_d");
char sliderAngleB1_d_buf[BUFLENSLIDER];
EmbAJAXSlider sliderAngleA1("sliderAngleA1", 0, 180, 90); EmbAJAXMutableSpan sliderAngleA1_d("sliderAngleA1_d");
char sliderAngleA1_d_buf[BUFLENSLIDER];

EmbAJAXCheckButton adjustServo1("adjustServo1", ""); EmbAJAXMutableSpan adjustServo1_d("adjustServo1_d");
EmbAJAXCheckButton ackAngleA1("AngleA1", ""); EmbAJAXMutableSpan ackAngleA1_d("ackAngleA1_d");
EmbAJAXCheckButton ackAngleB1("ackAngleB1", ""); EmbAJAXMutableSpan ackAngleB1_d("ackAngleB1_d");

/////////////////////////////////////////// fine adjust ///////////////////////////////////////////
int A1_count = 90;
void upA1Pressed(EmbAJAXPushButton*) {
  A1_count++;
}
EmbAJAXPushButton upA1("upA1", "up", upA1Pressed);
EmbAJAXMutableSpan upA1_d("upA1_d");
char upA1_d_buf[BUFLENSLIDER];
void downA1Pressed(EmbAJAXPushButton*) {
  A1_count--;
}
EmbAJAXPushButton downA1("downA1", "down", downA1Pressed);
EmbAJAXMutableSpan downA1_d("downA1_d");
char downA1_d_buf[BUFLENSLIDER];
EmbAJAXCheckButton takeA1("takeA1", ""); EmbAJAXMutableSpan takeA1_d("takeA1_d");

int B1_count = 90;
void upB1Pressed(EmbAJAXPushButton*) {
  B1_count++;
}
EmbAJAXPushButton upB1("upB1", "up", upB1Pressed);
EmbAJAXMutableSpan upB1_d("upB1_d");
char upB1_d_buf[BUFLENSLIDER];
void downB1Pressed(EmbAJAXPushButton*) {
  B1_count--;
}
EmbAJAXPushButton downB1("downB1", "down", downB1Pressed);
EmbAJAXMutableSpan downB1_d("downB1_d");
char downB1_d_buf[BUFLENSLIDER];
EmbAJAXCheckButton takeB1("takeB1", ""); EmbAJAXMutableSpan takeB1_d("takeB1_d");

int A2_count = 90;
void upA2Pressed(EmbAJAXPushButton*) {
  A2_count++;
}
EmbAJAXPushButton upA2("upA2", "up", upA2Pressed);
EmbAJAXMutableSpan upA2_d("upA2_d");
char upA2_d_buf[BUFLENSLIDER];
void downA2Pressed(EmbAJAXPushButton*) {
  A2_count--;
}
EmbAJAXPushButton downA2("downA2", "down", downA2Pressed);
EmbAJAXMutableSpan downA2_d("downA2_d");
char downA2_d_buf[BUFLENSLIDER];
EmbAJAXCheckButton takeA2("takeA2", ""); EmbAJAXMutableSpan takeA2_d("takeA2_d");

int B2_count = 90;
void upB2Pressed(EmbAJAXPushButton*) {
  B2_count++;
}
EmbAJAXPushButton upB2("upB2", "up", upB2Pressed);
EmbAJAXMutableSpan upB2_d("upB2_d");
char upB2_d_buf[BUFLENSLIDER];
void downB2Pressed(EmbAJAXPushButton*) {
  B2_count--;
}
EmbAJAXPushButton downB2("downB2", "down", downB2Pressed);
EmbAJAXMutableSpan downB2_d("downB2_d");
char downB2_d_buf[BUFLENSLIDER];
EmbAJAXCheckButton takeB2("takeB2", ""); EmbAJAXMutableSpan takeB2_d("takeB2_d");

///////////////////////////////////////////// servo moving speeg //////////////////////////////////////////
EmbAJAXTextInput<BUFLENSRVSPD> srvSpd0("srvSpd0"); EmbAJAXMutableSpan srvSpd0_d("srvSpd0_d"); char srvSpd0_buf[BUFLENSRVSPD];
EmbAJAXTextInput<BUFLENSRVSPD> srvSpd1("srvSpd1"); EmbAJAXMutableSpan srvSpd1_d("srvSpd1_d"); char srvSpd1_buf[BUFLENSRVSPD];

///////////////////////////////////////////// servo2 //////////////////////////////////////////
EmbAJAXSlider sliderAngleB2("sliderAngleB2", 0, 180, 90); EmbAJAXMutableSpan sliderAngleB2_d("sliderAngleB2_d");
char sliderAngleB2_d_buf[BUFLENSLIDER];
EmbAJAXSlider sliderAngleA2("sliderAngleA2", 0, 180, 90); EmbAJAXMutableSpan sliderAngleA2_d("sliderAngleA2_d");
char sliderAngleA2_d_buf[BUFLENSLIDER];

EmbAJAXCheckButton adjustServo2("adjustServo2", ""); EmbAJAXMutableSpan adjustServo2_d("adjustServo2_d");
EmbAJAXCheckButton ackAngleA2("AngleA2", ""); EmbAJAXMutableSpan ackAngleA2_d("ackAngleA2_d");
EmbAJAXCheckButton ackAngleB2("ackAngleB2", ""); EmbAJAXMutableSpan ackAngleB2_d("ackAngleB2_d");

//////////////////////////////////////////////// swap servo angles //////////////////////////////////////////
EmbAJAXCheckButton swpServo0("swpServo0", ""); EmbAJAXMutableSpan swpServo0_d("swpServo0_d");
EmbAJAXCheckButton swpServo1("swpServo1", ""); EmbAJAXMutableSpan swpServo1_d("swpServo1_d");

/////////////////////////////////////// save acknowledgement /////////////////////////////////
EmbAJAXCheckButton checkGeneral("checkGeneral", ""); EmbAJAXMutableSpan checkGeneral_d("checkGeneral_d");
EmbAJAXCheckButton checkSingle("checkSingle", ""); EmbAJAXMutableSpan checkSingle_d("checkSingle_d");
EmbAJAXCheckButton checkDouble("checkDouble", ""); EmbAJAXMutableSpan checkDouble_d("checkDouble_d");
EmbAJAXCheckButton checkSensor("checkSensor", ""); EmbAJAXMutableSpan checkSensor_d("checkSensor_d");
EmbAJAXCheckButton checkOutput("checkOutput", ""); EmbAJAXMutableSpan checkOutput_d("checkOutput_d");
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

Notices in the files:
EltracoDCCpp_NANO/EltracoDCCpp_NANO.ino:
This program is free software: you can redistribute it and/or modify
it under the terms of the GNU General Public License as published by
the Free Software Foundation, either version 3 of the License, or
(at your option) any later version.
